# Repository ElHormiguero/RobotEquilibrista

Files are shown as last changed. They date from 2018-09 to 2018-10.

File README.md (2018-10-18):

# RobotEquilibrista
Los robots conocidos como robots auto balanceados o “self balancing robot” se caracterizan por mantener el equilibrio sobre dos ruedas, lo cual hace que el eje vertical sea inestable si no aplicamos un algoritmo de control. Tiene un acelerómetro y giróscopo para obtener el ángulo de la vertical, dos motores paso a paso que permiten saber a qué velocidad se mueven y cuanto se han desplazado, un chip de radiofrecuencia para el control remoto desde el mando y un microcontrolador.

El funcionamiento se basa en dos PID en cascada y un tercer controlador proporcional:

El primero de ellos tiene como entrada el ángulo del robot proporcionado por un acelerómetro, y como salida la aceleración de los motores, de forma que si aumenta el ángulo (se desestabiliza), acelera para que la propia inercia lo mantenga vertical. Realmente es un controlador PD, ya que la parte integral no es necesaria.
El segundo controlador trata de mantener la velocidad indicada por el usuario. Si solo mantenemos el controlador anterior, por muy calibrado que tengamos el ángulo cero, el robot tenderá a irse hacia uno u otro lado, por ello es necesario un PID que corrija el ángulo objetivo del controlador anterior en función de la velocidad actual, de esta forma ajustamos el ángulo deseado para mantener una velocidad. Este controlador no requiere de componente derivativa, por lo que es un PI.
FInalmente se ha integrado un controlador proporcional P que mantiene la posición del robot fija, actúa aplicando una velocidad objetivo al controlador anterior en función del error de posición, esto hace que al desplazarlo, vuelva a su posición inicial. Dicho controlador solo se utiliza en caso de no estar estableciendo una velocidad desde el mando.

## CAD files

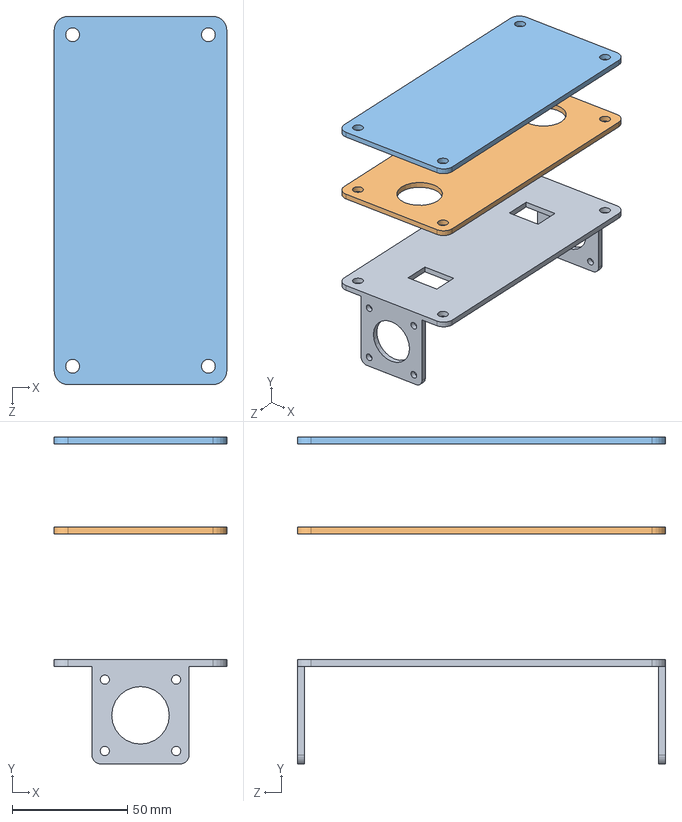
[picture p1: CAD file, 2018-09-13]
Piezas 3D/Ensamblaje.SLDASM
75.0 x 142.1 x 160.0 mm
Base inferior
Base intermedia
Base superior

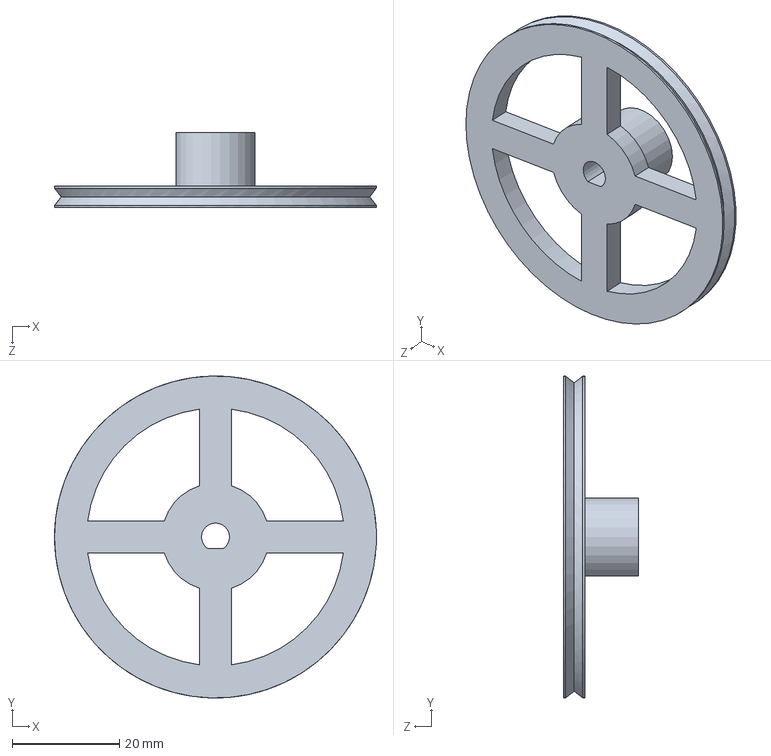
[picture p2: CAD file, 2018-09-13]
Piezas 3D/Rueda.SLDPRT
60.0 x 60.0 x 14.0 mm

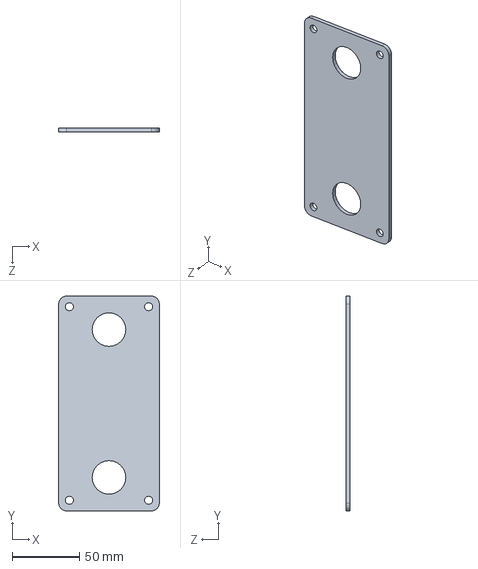
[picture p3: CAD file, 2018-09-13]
Piezas 3D/Base intermedia.SLDPRT
75.0 x 160.0 x 3.00 mm

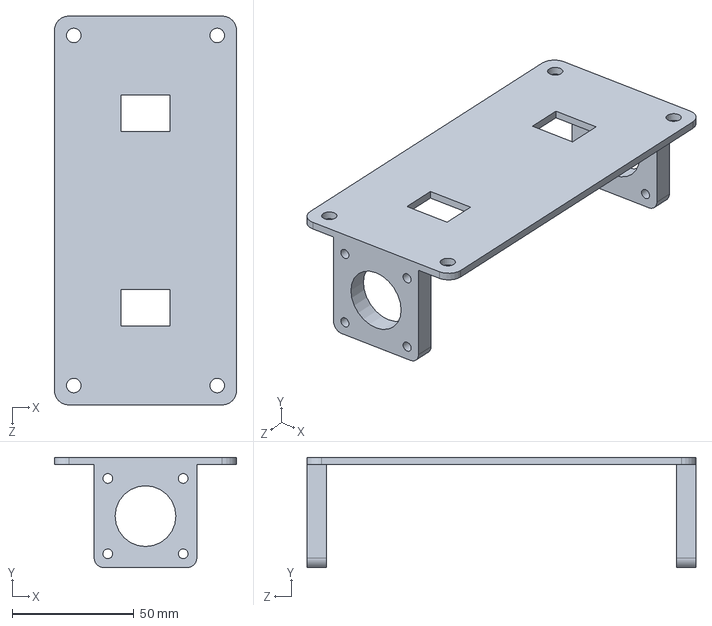
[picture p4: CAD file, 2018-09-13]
Piezas 3D/Base inferior.SLDPRT
75.0 x 45.3 x 160.0 mm

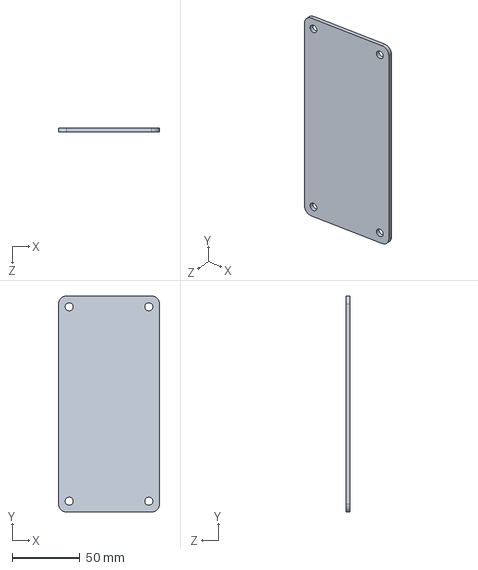
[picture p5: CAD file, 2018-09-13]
Piezas 3D/Base superior.SLDPRT
75.0 x 160.0 x 3.00 mm

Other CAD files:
Piezas 3D/STL/Base inferior.STL
Piezas 3D/STL/Base intermedia.STL
Piezas 3D/STL/Base superior.STL
Piezas 3D/STL/Rueda.STL

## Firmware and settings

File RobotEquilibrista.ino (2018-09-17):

/* Robot auto equilibrado con dos PID en cascada y un control de la posición. Programado sobre Arduino Leonarado (2 timer de 16 bits)
   Autor: Javier Vargas. El Hormiguero.
   https://creativecommons.org/licenses/by/4.0/
*/
//PINES
#define PinSTEP1 8
#define PinSTEP2 5
#define PinDIR1 9
#define PinDIR2 6
#define PinENABLE1 7
#define PinENABLE2 4
#define CE_PIN A0
#define CSN_PIN A1

//CONFIGURACION
//General
#define AnguloOFF 60 //Grados entorno a la vertical para desactivado de motores
#define AnguloOK 1 //Grados entorno a la vertical para activado de motores
//Cinemática
#define RadioRueda 3.25f //(cm) //Radio de la rueda
#define PasosVuelta 3200 //Pasos por vuelta del motor paso a paso
#define velocidadMax 120 //(cm/s)
#define velocidadMin 0.0001 //(cm/s)
#define DIRECCION1 HIGH //Rueda uno directa
#define DIRECCION2 LOW //Rueda dos invertida
//Control
#define Muestreo 25 //(ms) Periodo del algoritmo de control
#define Offset 4.5f //Offset del acelerometro
#define KfiltComp 0.99f //Constante del filtro complementario del acelerómetro y giróscopo
#define KfiltroRFvel 0.2 //Filtro del valor de velocidad obtenido por RF
#define KfiltroRFgiro 0.8 //Filtro del valor de giro obtenido por RF
#define TiempoControlX 1500 //(ms) Tiempo sin recibir por RF tras el que se activa el control de posicion 
double KpA = 17, KiA = 0, KdA = 3.5;  //Control PID del angulo --> Sin contrapeso mejor: KpA = 20, KiA = 0, KdA = 5;
double KpV = 0.15, KiV = 0.01, KdV = 0; //Control PID de la velocidad --> Sin contrapeso mejor: KpV = 0.12, KiV = 0.04, KdV = 0;
double KpX = 0.8; //Control proporcional de la posicion
float outMaxA = 400; //Acelercion maxima a la salida de PID del angulo
float outMaxV = 20; //Angulo maximo objetivo a la salida del PID de velocidad
float outMaxX = 30; //Velocidad objetivo máxima del control de posicion

//LIBRERIAS Y VARIABLES

//PID
#include <PID_v1.h>
double SetpointA, InputA, OutputA;
PID pidA(&InputA, &OutputA, &SetpointA, KpA, KiA, KdA, DIRECT);

double SetpointV, InputV, OutputV;
PID pidV(&InputV, &OutputV, &SetpointV, KpV, KiV, KdV, DIRECT);

//RADIOFRECUENCIA
byte direccion[5] = {'h', 'o', 'r', 'm', 'i'}; //Variable con la dirección del canal por donde se va a transmitir
#include <SPI.h>
#include <nRF24L01.h>
#include <RF24.h>
RF24 radio(CE_PIN, CSN_PIN);

//IMU
#include <MPU6050_CompFilter.h>
MPU6050_CompFilter mpu(0x68);

//TIMER
#include <TimerOne.h>
#include <TimerThree.h>

#include <digitalWriteFast.h> //Más rapido!
unsigned long m1, m2 = 0;
float Angulo = 0; //Angulo del robot
float AnguloObj = 0; //Angulo objetivo
float Velocidad = 0; //Velocidad del robot
float VelocidadObj = 0; //Velocidad objetivo
float Posicion = 0; //Posicion del robot
float PosicionObj = 0; //Posicion objetivo
float Aceleracion = 0; //Aceleracion del robot
float Giro = 0; //Nivel de giro del robot
float PPcm;
float datos[2];
unsigned long TimeMov = 0;

void setup() {

  //PinMode
  pinMode(PinSTEP1, OUTPUT);
  pinMode(PinSTEP2, OUTPUT);
  pinMode(PinDIR1, OUTPUT);
  pinMode(PinDIR2, OUTPUT);
  pinMode(PinENABLE1, OUTPUT);
  pinMode(PinENABLE2, OUTPUT);

  digitalWrite(PinENABLE1, HIGH);
  digitalWrite(PinENABLE2, HIGH);
  digitalWrite(PinDIR1, DIRECCION1);
  digitalWrite(PinDIR2, DIRECCION2);

  //IniciO IMU
  mpu.Iniciar((float)Muestreo / 1000);
  mpu.setKcompFilter(KfiltComp);

  //Inicio PID
  pidA.SetTunings(KpA, KiA, KdA);
  pidA.SetOutputLimits(-outMaxA, outMaxA);
  pidA.SetMode(AUTOMATIC);

  pidV.SetTunings(KpV, KiV, KdV);
  pidV.SetOutputLimits(-outMaxV, outMaxV);
  pidV.SetMode(AUTOMATIC);

  //inicio NRF24L01
  radio.begin();
  radio.openReadingPipe(1, direccion);
  radio.startListening();   //empezamos a escuchar por el canal

  //Inicio TIMER
  Timer1.initialize(250000);
  Timer1.attachInterrupt(Step1);
  Timer1.stop();

  Timer3.initialize(250000);
  Timer3.attachInterrupt(Step2);
  Timer3.stop();

  PPcm = (float)PasosVuelta / (2 * PI * RadioRueda); //Pasos por centímetro recorrido

  delay(1000);
}

////////////////////
////////LOOP////////
////////////////////

void loop() {
  //Loop cada periodo de muestreo
  if (m1 != millis() / Muestreo) {
    m1 = millis() / Muestreo;

    ObtenerAngulo(); //Lectura de la IMU

    //ROBOT EN POSICION VERTICAL
    if (RobotVerticalOK()) {
      ControlRemoto(); //Recibe la velocidad y el giro por RF
      ControlPosicion();  //Tras cierto tiempo sin recibir orden por RF mantiene la posicion
      ControlVelocidad(); //PID para ajustar el angulo objetivo y mantener la velocidad
      ControlEquilibrio(); //PID para ajustar la aceleracion de las ruedas y mantener el equilibrio
    }

    //ROBOT HORIZONTAL
    else {
      MotoresOFF(); //Apaga los motores 
      ReiniciarPID(); //Reinicia los controladores PID
    }

  }
}

////////////////////
////////////////////
////////////////////

void ReiniciarPID() {
  pidA.SetOutputLimits(0.0, 1.0);  //Fuerza el máximo a 0
  pidA.SetOutputLimits(-1.0, 0.0);  //Fuerza el minimo a 0
  pidA.SetOutputLimits(-outMaxA, outMaxA);
  pidV.SetOutputLimits(0.0, 1.0);  //Fuerza el máximo a 0
  pidV.SetOutputLimits(-1.0, 0.0);  //Fuerza el minimo a 0
  pidV.SetOutputLimits(-outMaxV, outMaxV);
}

void MotoresOFF() {
  Velocidad = 0;
  Posicion = 0;
  PosicionObj = 0;
  SetVelocidad(0, 0);
}

boolean RobotVerticalOK() {
  static boolean VerticalOK = 0;

  //El robot se encuentra en posicion correcta
  if (VerticalOK) {
    if (abs(Angulo) > AnguloOFF) {
      //Angulo de caida superado
      VerticalOK = 0;
    }
  }

  //El robot no se encuentra totalmente vertical
  else {
    if (abs(Angulo) < AnguloOK) {
      //Angulo de posicion correcta superado
      VerticalOK = 1;
    }
  }

  return VerticalOK;
}

void ControlRemoto() {
  static float datosFilt[2];

  if (radio.available()) {
    //Recepcion por RF
    radio.read(datos, sizeof(datos));
    //Filtrado de los datos
    datosFilt[1] = (KfiltroRFvel * datos[1] + (1 - KfiltroRFvel) * datosFilt[1]);
    datosFilt[0] = (KfiltroRFgiro * datos[0] + (1 - KfiltroRFgiro) * datosFilt[0]);
    //Interpretacion de velocidad y giro
    VelocidadObj = datosFilt[1] / 2;
    Giro = datosFilt[0] / 5;
    //Actualizacion del contador (quita el control de posicion)
    if (abs(VelocidadObj) > 5 || abs(Giro) > 2) TimeMov = millis();
  }
}

void ObtenerAngulo() {
  //Lectura del acelerometro
  mpu.Lectura(1, 0); //Eje x
  Angulo = mpu.angX() + Offset;
}

void ControlPosicion() {
  static boolean e = 0;
  if (millis() > TimeMov + TiempoControlX) {
    if (!e) PosicionObj = Posicion, e = 1; //Marcamos la posicion a mantener
    VelocidadObj = KpX * (PosicionObj - Posicion); //Control proporcional de la posicion tras cierto tiempo sin recibir RF 
    VelocidadObj = constrain(VelocidadObj, -outMaxX, outMaxX);
    Giro = 0;
  }
  else if (e) e = 0;
}

void ControlVelocidad() {
  //Control PID del angulo objetivo a partir de la velocidad
  SetpointV = VelocidadObj; //Consigna la velocidad objetivo
  InputV = Velocidad; //Entrada la velocidad objetivo
  pidV.Compute();
  AnguloObj = -OutputV; //La salida es el angulo objetivo del siguiente PID
}

void ControlEquilibrio() {
  //Control PID del angulo
  SetpointA = AnguloObj; //Consigna el angulo objetivo
  InputA = Angulo; //Entrada el angulo del robot
  pidA.Compute();
  Aceleracion = OutputA; //Salida la aceleracion

  //Calculo de la velocidad
  Velocidad += Aceleracion * (float)Muestreo / 1000;

  //Posicion del robot
  Posicion += Velocidad * (float)Muestreo / 1000;

  //Salida aplicada a la velocidad de las ruedas
  float v1 = Velocidad + Giro; //Velocidad rueda izquierda
  float v2 = Velocidad - Giro; //Velocidad rueda derecha
  SetVelocidad(v1, v2);
}

void SetVelocidad(float v1, float v2) {
  static volatile boolean e1, e2 = 0; //Estado de los timers
  static volatile boolean d1 = 1;
  static volatile boolean d2 = 1; //Direccion de los motores

  //Limite de velocidad entre los limites de velocidad maxima
  v1 = constrain(v1, -velocidadMax, velocidadMax);
  v2 = constrain(v2, -velocidadMax, velocidadMax);

  //Direccion motor 1
  if (v1 >= 0) {
    if (!d1) {
      d1 = 1;
      digitalWriteFast(PinDIR1, DIRECCION1);
    }
  }
  else if (d1) {
    d1 = 0;
    digitalWriteFast(PinDIR1, !DIRECCION1);
  }

  //Direccion motor 2
  if (v2 >= 0) {
    if (!d2) {
      d2 = 1;
      digitalWriteFast(PinDIR2, DIRECCION2);
    }
  }
  else if (d2) {
    d2 = 0;
    digitalWriteFast(PinDIR2, !DIRECCION2);
  }

  //Velocidad motor 1
  if (abs(v1) >= velocidadMin) {
    unsigned long T1 = 500000 / (abs(v1) * PPcm); //Periodo de un semipulso
    if (!e1) { //Inicia el timer
      Timer1.start();
      digitalWriteFast(PinENABLE1, LOW); //Activa el motor
      e1 = 1;
    }
    Timer1.setPeriod(T1); //Periodo de la interrpucion
  }
  else if (e1) { //Desactiva el timer
    Timer1.stop();
    digitalWriteFast(PinENABLE1, HIGH); //Desactiva el motor
    e1 = 0;
  }

  //Velocidad motor 2
  if (abs(v2) >= velocidadMin) {
    unsigned long T2 = 500000 / (abs(v2) * PPcm); //Periodo de un semipulso
    if (!e2) {  //Inicia el timer
      Timer3.start();
      digitalWriteFast(PinENABLE2, LOW); //Activa el motor
      e2 = 1;
    }
    Timer3.setPeriod(T2); //Periodo de la interrpucion
  }
  else if (e2) { //Desactiva el timer
    Timer3.stop();
    digitalWriteFast(PinENABLE2, HIGH); //Desactiva el motor
    e2 = 0;
  }

}

//STEP

void Step1() {
  static volatile boolean e = 0;
  if (e) {
    digitalWriteFast(PinSTEP1, LOW);
    e = 0;
  }
  else {
    digitalWriteFast(PinSTEP1, HIGH);
    e = 1;
  }
}

void Step2() {
  static volatile boolean e = 0;
  if (e) {
    digitalWriteFast(PinSTEP2, LOW);
    e = 0;
  }
  else {
    digitalWriteFast(PinSTEP2, HIGH);
    e = 1;
  }
}

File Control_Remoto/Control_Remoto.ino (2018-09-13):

/*Control remoto con Gamepad Shield para Arduino, comunicacion con el chip NRF2401L.
  Autor: Javier Vargas. El Hormiguero.
  https://creativecommons.org/licenses/by/4.0/
*/

//Pines
#define Pin_xJoystic A0
#define Pin_yJoystic A1
#define Pin_BotonA 2
#define Pin_BotonB 3
#define Pin_BotonC 4
#define Pin_BotonD 5

//CONFIGURACION
#define V3_3 //Módulo conectado a 3.3V (descomentar en caso contrario)
#define RangoJoystic 100 //Rango de salida de lectura del joystic
#define OffsetX 7
#define OffsetY 0

//Variable con la dirección del canal por donde se va a transmitir
byte direccion[5] = {'h', 'o', 'r', 'm', 'i'};

//NRF24L01
#define CE_PIN 9
#define CSN_PIN 10
#include <SPI.h>
#include <nRF24L01.h>
#include <RF24.h>
RF24 radio(CE_PIN, CSN_PIN);

//Variables del mando
int MaxADC = 1023;
float datos[2];

void setup() {

  Serial.begin(115200);

  //PinMode
  pinMode(Pin_BotonA, INPUT_PULLUP);
  pinMode(Pin_BotonB, INPUT_PULLUP);
  pinMode(Pin_BotonC, INPUT_PULLUP);
  pinMode(Pin_BotonD, INPUT_PULLUP);

  //inicializamos el NRF24L01
  radio.begin();
  radio.openWritingPipe(direccion);

  //Entrada analógica máxima
#ifdef V3_3
  MaxADC = (float)(3.33 / 5) * 1023;
#else
  MaxADC = 1023;
#endif
}

void loop() {
  datos[0] = JoysticX();
  datos[1] = JoysticY();
  radio.write(datos, sizeof(datos));
  Serial.print(datos[0]);
  Serial.print(" / ");
  Serial.println(datos[1]);
  delay(100);
}

int JoysticX() {
  int x_Joystic;
  x_Joystic = map(analogRead(Pin_xJoystic) + OffsetX, 0, MaxADC, -RangoJoystic, RangoJoystic);
  x_Joystic = constrain(x_Joystic, -RangoJoystic, RangoJoystic);
  return x_Joystic;
}

int JoysticY() {
  int y_Joystic;
  y_Joystic = map(analogRead(Pin_yJoystic) + OffsetY, 0, MaxADC, -RangoJoystic, RangoJoystic);
  y_Joystic = constrain(y_Joystic, -RangoJoystic, RangoJoystic);
  return y_Joystic;
}

boolean BotonA() {
  return !digitalRead(Pin_BotonA);
}

boolean BotonB() {
  return !digitalRead(Pin_BotonB);
}

boolean BotonC() {
  return !digitalRead(Pin_BotonC);
}

boolean BotonD() {
  return !digitalRead(Pin_BotonD);
}
